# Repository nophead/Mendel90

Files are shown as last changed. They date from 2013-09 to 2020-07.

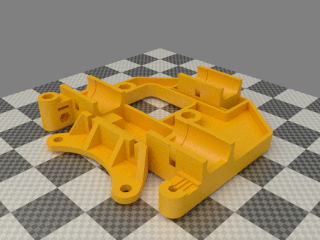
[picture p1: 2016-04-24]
dibond/render/printed/x_carriage_parts.png

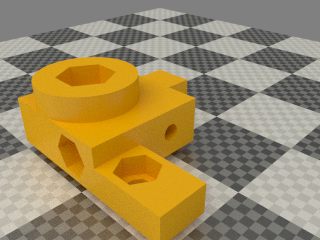
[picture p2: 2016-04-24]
dibond/render/printed/cal.png

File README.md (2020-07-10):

# A RepRap Mendel variant using sheets for the frame instead of rods

## Standard variants
[dibond](https://github.com/nophead/Mendel90/tree/master/dibond) is the version that was sold as a kit with 3mm sheets, 8mm rods and uses nuts and machine screws through the frame.

[sturdy](https://github.com/nophead/Mendel90/tree/master/sturdy) is 12mm MDF sheets, 10mm rods and uses wood screws into pilot holes in the frame. It can be built without CNC.

[mendel](https://github.com/nophead/Mendel90/tree/master/mendel) is 6mm acrylic sheets with a 10mm acrylic base, 8mm rods and uses machine screws into tapped holes in the frame.

[huxley](https://github.com/nophead/Mendel90/tree/master/huxley) is a scaled down version of dibond using 6mm rods and NEMA14 motors.

The dibond, sturdy and mendel versions can be modified to accept the E3D v6 hot end. The files that change are [dibond_E3D](https://github.com/nophead/Mendel90/tree/master/dibond_E3D)
and [sturdy_E3D](https://github.com/nophead/Mendel90/tree/master/sturdy_E3D).

## Limitations
The dibond and sturdy versions are well tested and popular. The acrylic version, called mendel, hasn't been built for a long time and is not recommened.
The Huxley version hasn't been tested in its final form although one prototype has been made of an earlier version and a few snags fixed since.

## Use
Add the directory of the OpenScad executable to your search path. OpenSCAD-2015.05 or later is required.
To get PDF versions of the sheet drawings add InkScape to your search path.

To make all the files for a machine run
```python
make_machine.py machine_name
```

To make just the bom, sheets or stls run bom.py, sheets.py or stls.py machine\_name.

machine\_name can be dibond, mendel, sturdy or huxley. To make your own variant copy scad\conf\mendel\_config.scad or scad\conf\sturdy\_config.scad to yourname\_config.scad.  Then run `make_machine.py yourname`.

To view the model of the whole machine, open scad\main.scad. It will take several minutes to render (about about 5 minutes on my computer) but after that you can pan and zoom it at reasonable speed and changes takes less time to render.  (Note: main.scad will only render correctly if conf\machine.scad exists, which is created by the make_machine.py script.)

To view a sub-assembly, open the individual scad files. Set the exploded flag in config.scad to make exploded views.

To get blender renders of all the parts put blender in your search path and run `render.py machine_name`.

## Credits
Fan model based on [this model](http://www.thingiverse.com/thing:8063) by MiseryBot, CC license.

[Sanguinololu model](http://www.thingiverse.com/thing:18606) by ax\_the\_b, CC license.

Spring taken from openscad example 20

x-end.scad and wade.scad use some elements of the Prusa ones by Josef Prusa, GPL license.

z_couplings originally based on [this model](http://www.thingiverse.com/thing:7153) by Griffin_Nicoll, GPL license.

Bearing holders originally based on [this model](http://www.thingiverse.com/thing:7755) by Jolijar, CC license.

InkCL.py based on [this code](http://kaioa.com/node/42)

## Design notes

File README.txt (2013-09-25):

Limitations
-----------
Currently only supports mendel and sturdy machine variants, the huxley version needs more work.

Use
---
Add the directory of the OpenScad executable to your search path. OpenSCAD-2013.06 or later is required.
To get PDF versions of the sheet drawings add InkScape to your search path.

To make all the files for a machine run
    make_machine.py machine_name

To make just the bom, sheets or stls run bom.py, sheets.py or stls.py machine_name.

machine_name can be mendel or sturdy. To make your own variant copy scad\conf\mendel_config.scad or scad\conf\sturdy_config.scad to yourname_config.scad.  Then run make_machine yourname.

To view the model of the whole machine, open scad\main.scad. It will take several minutes to render (about about 8 minutes on my computer) but after that you can pan and zoom it at reasonable speed and changes takes less time to render.  (Note: main.scad will only render correctly if conf\machine.scad exists, which is created by the make_machine.py script.)

To view a sub-assembly, open the individual scad files. Set the exploded flag in config.scad to make exploded views.

To get blender renders of all the parts put blender in your search path and run render.py machine_name.

Credits
-------
Fan model based on http://www.thingiverse.com/thing:8063 by MiseryBot, CC license.

Sanguinololu model http://www.thingiverse.com/thing:18606 by ax_the_b, CC license.

Spring taken from openscad example 20

x-end.scad and wade.scad use some elements of the Prusa ones by Josef Prusa, GPL license.

z_couplings originally based on http://www.thingiverse.com/thing:7153 by Griffin_Nicoll, GPL license.

Bearing holders originally based on http://www.thingiverse.com/thing:7755 by Jolijar, CC license.

InkCL.py based on code from http://kaioa.com/node/42

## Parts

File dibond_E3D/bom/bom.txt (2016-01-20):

Vitamins:
          E                                                      
          x                                                      
          t                                                      
          r                                                      
          u                                                      
          d                                                      
          e                                                      
          r                                                      
                                                                 
          c  E                          X                        
          o  x                                                   
          n  t                 S        c                        
    E     n  r                 p        a                        
    l     e  u                 o     X  r           Y            
    e     c  d           P     o        r                        
    c  E  t  e           r     l     c  i           c            
 B  t  x  i  r     H  M  i           a  a  X  X     a  Y  Y     Z
 e  r  t  o        o  a  n     h  X  r  g        Y  r        Z   
 d  o  r  n  m  F  t  c  t     o     r  e  i  m     r  i  m     m
    n  u     o  r     h        l  a  i     d  o  a  i  d  o  a  o
 f  i  d  p  t  a  e  i  b  P  d  x  a  f  l  t  x  a  l  t  x  t
 a  c  e  c  o  m  n  n  e  s  e  i  g  a  e  o  i  g  e  o  i  o
 n  s  r  b  r  e  d  e  d  u  r  s  e  n  r  r  s  e  r  r  s  r
  |  |  |  |  |  |  |  |  | 1|  |  |  |  |  |  |  |  |  |  |  |  |  1 THS15 Aluminium clad resistor 10R
  |  |  |  |  |  |  |  |  | 1|  |  |  |  |  |  |  |  |  |  |  |  |  1 THS15 Aluminium clad resistor 4R7
  |  |  |  |  |  |  |  |  | 1|  |  |  |  |  |  |  |  |  |  |  |  |  1 PSU e.g. ALPINE500
  |  | 3|  |  |  |  |  |  |  | 4|  |  |  |  |  |  |  |  |  |  |  |  7 Ball bearing 608 8mm x 22mm x 7mm
  |  |  |  |  |  |  |  |  |  |  |  |  |  | 2|  |  |  | 2|  |  |  |  4 Ball bearing 624 4mm x 13mm x 5mm
  |  |  |  |  |  |  |  | 4|  |  |  |  |  |  |  |  |  |  |  |  |  |  4 19mm bulldog clip
  |  |  |  |  |  |  |  | 1|  |  |  |  |  |  |  |  |  |  |  |  |  |  1 PCB bed 214mm x 214mm
  |  |  |  |  |  |  |  |  |  |  |  |  |  |  |  | 1|  |  |  |  |  |  1 Belt T2 x 6mm x 662mm
  |  |  |  |  |  |  |  |  |  |  | 1|  |  |  |  |  |  |  |  |  |  |  1 Belt T2 x 6mm x 860mm
  |  |  |  |  |  |  |  | 4|  |  |  |  |  |  |  |  |  |  |  |  |  |  4 Corrugated cardboard 201mm x 216mm x 5mm
  |  |  |  |  |  |  |  | 4|  |  |  |  |  |  |  |  |  |  |  |  |  |  4 M3 cap screw x 10mm
  |  | 3|  |  |  |  |  |  |  |  |  |  |  |  |  |  |  |  |  |  |  |  3 M3 cap screw x 12mm
  | 4|  |  |  |  |  |  |  |  |  |  | 2|  |  | 6| 4|14|  |  | 2| 2| 34 M3 cap screw x 16mm
  |  |  |  |  |  |  |  |  |  |  |  | 1|  | 8|10|  | 2|  |  |  | 8| 29 M3 cap screw x 20mm
  |  |  |  |  |  |  |  |  |  |  |  | 2|  |  |  |  |  |  |  |  |  |  2 M3 cap screw x 25mm
  |  |  |  | 2|  |  |  |  |  |  |  |  |  |  | 2|  |  |  |  |  |  |  4 M3 cap screw x 45mm
 4|  |  |  |  |36|  |  |  | 4| 2|  |  |  |  |  | 8|  | 1| 4| 4| 4| 67 M4 cap screw x 16mm
  |  |  |  |  |  |  |  |  |  |  |  |  | 4|  |  |  |  | 1|  |  |  |  5 M4 cap screw x 30mm
  |  |  |  |  |  |  |  |  |  |  |  |  |  | 1|  |  |  |  |  |  |  |  1 M4 cap screw x 45mm
  |  |  |  |  |  |  |  |  |  | 4|  |  |  |  |  |  |  |  |  |  |  |  4 M8 cap screw x 30mm
  |  |  |  |  | 2|  |  |  |  |  |  |  |  |  |  |  |  |  |  |  |  |  2 Dibond sheet 166mm x 388mm x 3mm
  |  |  |  |  |  |  |  |  |  |  |  |  |  |  |  |  | 1|  |  |  |  |  1 Dibond sheet 216mm x 216mm x 3mm
  |  |  |  |  | 1|  |  |  |  |  |  |  |  |  |  |  |  |  |  |  |  |  1 Dibond sheet 465mm x 388mm x 3mm
  |  |  |  |  | 1|  |  |  |  |  |  |  |  |  |  |  |  |  |  |  |  |  1 Dibond sheet 465mm x 419mm x 3mm
  |  |  | 1|  |  |  |  |  |  |  |  |  |  |  |  |  |  |  |  |  |  |  1 15 way D PCB mount plug
  |  |  |  |  |  |  |  |  |  |  |  |  |  |  | 1|  |  |  |  |  |  |  1 15 way D IDC socket
  |  |  |  |  |  | 1|  |  |  |  |  |  |  |  |  |  |  |  |  |  |  |  1 Fan 30mm x 10mm
  |  |  |  |  |  |  |  |  |  |  |  |  | 1|  |  |  |  |  |  |  |  |  1 Fan 60mm x 15mm
  |  |  |  |  |  |  |  |  |  | 1|  |  |  |  |  |  |  |  |  |  |  |  1 Foam sponge 20mm x 20mm x 20mm
  |  |  |  | 1|  |  |  |  |  |  |  |  |  |  | 2|  |  |  | 2|  |  |  5 M3 grub screw x 6mm
  |  |  |  |  |  |  |  | 1|  |  |  |  |  |  |  |  |  |  |  |  |  |  1 Glass sheet 214mm x 202mm x 2mm
  |  |  |  |  |  | 1|  |  |  |  |  |  |  |  |  |  |  |  |  |  |  |  1 E3D V6 direct 3mm
  |  |  |  |  |  |  |  | 4|  |  |  |  |  |  |  |  |  |  |  |  |  |  4 Hex male / female pillar M3 x 20mm
  |  | 3|  |  |  |  |  |  |  |  |  |  |  |  |  |  |  |  |  |  |  |  3 M3 hex screw x 10mm
  |  | 1|  |  |  |  |  |  |  |  | 1|  |  |  |  |  |  |  |  |  |  |  2 M4 hex screw x 20mm
  |  | 2|  |  |  |  |  |  |  |  |  |  |  |  |  |  |  |  |  |  |  |  2 M4 hex screw x 50mm
  |  | 1|  |  |  |  |  |  |  |  |  |  |  |  |  |  |  |  |  |  |  |  1 M8 hex screw x 60mm, hobbed at 25
  |  |  |  |  |  |  |  |  | 1|  |  |  |  |  |  |  |  |  |  |  |  |  1 IEC mains lead
  |  |  |  |  |  |  |  |  |  |  |  | 3|  | 2| 2|  | 3|  |  |  |  | 10 LM8UU linear bearing
  | 1|  |  |  |  |  |  |  |  |  |  |  |  |  |  |  |  |  |  |  |  |  1 Melzi electronics
  |  |  | 1|  |  |  |  |  |  |  |  |  |  |  |  |  |  |  |  |  |  |  1 2 way Molex KK header
  |  |  | 1|  |  |  |  |  |  |  |  |  |  |  |  |  |  |  |  |  |  |  1 3 way Molex KK header
  |  |  |  | 1|  |  |  |  |  |  |  |  |  |  | 1|  |  |  | 1|  | 2|  5 NEMA17 x 47mm stepper motor
  |  |  |  |  |  |  |  |  |  |  |  |  |  |  |  |  |  |  |  | 2|  |  2 Brass nut M6
  |  | 3|  | 3|  |  |  |  |  |  |  | 1|  |  |  |  |  |  |  |  |  |  7 Nut M3
  |  | 3|  |  |  |  |  |  |  |  |  |  |  |  |  |  |  |  |  |  |  |  3 Nut M4
  |  | 2|  |  |  |  |  |  |  |  |  |  |  |  |  |  |  |  |  |  |  |  2 Nut M8
  |  |  |  |  |  |  |  |  | 4|  |  |  |  |  |  |  |  |  |  |  |  |  4 Nyloc nut M2.5
  | 4|  |  |  |  |  |  |  |  |  |  | 4|  | 8|14| 4|16|  |  | 2|10| 62 Nyloc nut M3
 4|  |  |  |  |36|  |  |  | 4| 2|  |  | 4| 1|  | 8|  | 2| 4| 4| 4| 73 Nyloc nut M4
  |  |  |  |  |  |  |  |  |  | 4|  |  |  |  |  |  |  |  |  |  |  |  4 Nyloc nut M8
  |  |  |  |  |  |  |  |  |  |  |  |  |  |  | 2|  |  |  |  |  |  |  2 Nitrile O-ring 2.5mm x 1.6mm
  |  |  | 1|  |  |  |  |  |  |  |  |  |  |  |  |  |  |  |  |  |  |  1 Extruder connection PCB
  |  |  |  |  |  |  |  |  |  | 1|  |  |  |  |  |  |  |  |  |  |  |  1 PLA sample 3mm ~50m
  |  |  |  |  |  |  |  |  |  |  |  |  |  |  | 1|  |  |  |  |  |  |  1 Polypropylene strip 394mm x 18mm x 0.5mm
  |  |  |  |  |  |  |  |  |  |  |  |  |  |  | 1|  |  |  |  |  |  |  1 Polypropylene strip 456mm x 25mm x 0.5mm
  |  |  |  |  |  |  |  | 1|  |  |  |  |  |  |  |  |  |  |  |  |  |  1 Polypropylene strip 271mm x 33mm x 0.5mm
  |  |  |  |  |  |  |  |  | 4|  |  |  |  |  |  |  |  |  |  |  |  |  4 M2.5 pan screw x 12mm
  |  |  |  |  |  |  |  |  |  |  |  |  |  |  | 2|  |  |  | 4|  | 8| 14 M3 pan screw x 8mm
  |  |  |  |  |  |  |  |  | 2|  |  |  |  |  |  |  |  |  |  |  |  |  2 6-32 pan screw x 9.5mm
  |  |  |  | 2|  |  |  |  |  |  |  |  |  |  | 4| 2|  |  |  | 2|  | 10 No2 pan wood screw x 13mm
  |  |  |  |  |  |  |  |  |  |  |  |  |  |  | 1|  |  |  | 1|  |  |  2 GT2 pulley 20 teeth
  |  |  |  |  |  |  |  |  |  |  |  |  |  |  | 1|  |  |  |  |  |  |  1 Ribbon cable 20 way 1220mm
  |  |  |  |  |  |  |  | 1|  |  |  |  |  |  |  |  |  |  |  |  |  |  1 Ribbon cable 26 way 381mm
  |  | 1|  |  |  |  |  |  |  |  |  |  |  |  |  |  |  |  |  |  |  |  1 Smooth rod 8mm x 22mm
  |  |  |  |  |  |  |  |  |  |  |  |  |  |  |  | 1|  |  |  |  |  |  1 Smooth rod 8mm x 270mm
  |  |  |  |  |  |  |  |  |  |  |  |  |  |  |  |  |  |  |  | 2|  |  2 Smooth rod 8mm x 340mm
  |  |  |  |  |  |  |  |  |  |  | 2|  |  |  |  |  |  |  |  |  |  |  2 Smooth rod 8mm x 381mm
  |  |  |  |  |  |  |  |  |  |  |  |  |  |  |  | 1|  |  |  |  |  |  1 Smooth rod 8mm x 417mm
  | 1|  |  |  |  |  |  |  |  |  |  |  |  |  |  |  |  |  |  |  |  |  1 Micro SD card
  | 1|  |  |  |  |  |  |  |  |  |  |  |  |  |  |  |  |  |  |  |  |  1 Micro SD to USB adapter
  |  |  |  |  |  |  |  |  |  |  |  |  |  |  | 1| 1|  |  |  | 1|  |  3 Microswitch
  |  | 2|  |  |  |  |  |  |  |  |  |  |  |  |  |  |  |  |  |  |  |  2 Spring 7mm OD, 1mm gauge x 10mm long
  |  |  |  |  | 2|  |  |  |  |  |  |  |  |  |  |  |  |  |  |  |  |  2 AL square tube 12.7 x 12.7 x 1.63 x 400mm
  |  |  |  |  |  |  |  |  |  |  |  |  |  |  |  |  |  |  |  | 2|  |  2 Threaded rod M6 x 300mm
  |  |  |  |  |  |  |  |  | 1|  |  |  |  |  |  |  |  |  |  |  |  |  1 Heatshrink sleeving ID 10mm x 15mm
  |  |  |  |  |  |  |  | 2|  |  |  |  |  |  |  |  |  |  |  |  |  |  2 Heatshrink sleeving ID 1.6mm x 15mm
  | 2|  |  |  |  |  |  | 2| 3|  |  |  |  |  | 4|  |  |  |  |  |  | 11 Heatshrink sleeving ID 2.4mm x 15mm
  |  |  |  |  |  |  |  |  | 5|  |  |  |  |  |  |  |  |  |  |  |  |  5 Heatshrink sleeving ID 3.2mm x 15mm
  |  |  |  |  |  |  |  |  |  | 1|  |  |  |  |  |  |  |  |  |  |  |  1 PTFE tubing OD 4.6mm ID 3.84mm x 750mm
  |  |  |  |  |  |  |  |  | 2|  |  |  |  |  |  |  |  |  |  |  |  |  2 Heatshrink sleeving ID 6.4mm x 15mm
  |  |  |  |  |  |  |  | 2|  |  |  |  |  |  |  |  |  |  |  |  |  |  2 Heatshrink sleeving ID 6.4mm x 30mm
  |  |  |  |  |  | 1|  |  |  |  |  |  |  |  |  |  |  |  |  |  |  |  1 Heatshrink sleeving ID 6.4mm x 60mm
  |  |  |  |  |  |  |  |  |  |  |  |  |  |  |  |  |  |  |  |  | 2|  2 Neoprene tubing OD 8mm ID 5mm x 16mm
  |  |  | 2|  |  |  |  |  |  |  |  |  |  |  |  |  |  |  |  |  |  |  2 4 way terminal block
  |  |  |  |  |  |  |  | 1|  |  |  |  |  |  |  |  |  |  |  |  |  |  1 Epcos B57861S104F40 100K 1% thermistor
  | 1|  |  |  |  |  |  |  |  |  |  |  |  |  |  |  |  |  |  |  |  |  1 USB A to Mini B lead
  |  |  |  | 2|  |  |  |  | 4|  |  |  |  |  | 4| 2|  |  |  | 2|  | 14 Washer M2.5 x 5.9mm x 0.5mm
  | 8| 3|  | 2|  |  |  | 4|  |  |  | 4|  | 8|22| 4|16|  | 4| 2|18| 95 Washer M3 x 7mm x 0.5mm
 4|  | 8|  |  |40|  |  |  | 6| 2|  |  | 4| 2|  | 8|  | 5| 4| 4| 4| 91 Washer M4 x 9mm x 0.8mm
  |  |  |  |  |  |  |  |  |  |  |  |  |  | 2|  |  |  | 2|  |  |  |  4 Washer M5 x 20mm x 1.4mm
  |  |  |  |  |  |  |  |  |  |12|  |  |  |  |  |  |  |  |  |  |  | 12 Washer M8 x 17mm x 1.6mm
  |  |  |  |  |  |  |  |  |  | 4|  |  |  |  |  |  |  |  |  |  |  |  4 Washer M8 x 30mm x 1.5mm
  |  |  |  |  |  |  |  |  |  |  | 1|  |  |  |  |  |  |  |  |  |  |  1 Wingnut M4
  |  |  |  |  |  |  |  | 1|  |  |  |  |  |  |  |  |  |  |  |  |  |  1 Black wire 32/0.2 length 635mm
  |  |  |  |  |  |  |  | 1|  |  |  |  |  |  |  |  |  |  |  |  |  |  1 Red wire 32/0.2 length 620mm
  |  | 6|  |  |  |  |  |  |  |  |  |  |  |  | 2|  |  |  | 4|  | 8| 20 Star washer M3 x 0.5mm
  |  |  |  |  |  |  |  |  | 2|  |  |  |  |  |  |  |  |  |  |  |  |  2 Star washer M4 x 0.8mm
  |  | 1|  |  |  |  |  |  |  |  |  |  |  |  |  |  |  |  |  |  |  |  1 Star washer M8 x 1.6mm
  |  |  |  |  |10| 1|  |  | 2|  |  | 3|  |  |  |  | 3|  |  |  |  | 19 Ziptie 100mm min length

Printed:
  |  |  |  |  |  |  |  |  | 1|  |  |  |  |  |  |  |  |  |  |  |  |  1 atx_long_bracket.stl
  |  |  |  |  |  |  |  |  | 1|  |  |  |  |  |  |  |  |  |  |  |  |  1 atx_short_bracket.stl
  |  |  |  | 1|  |  |  |  |  |  |  |  |  |  |  |  |  |  |  |  |  |  1 d_motor_bracket.stl
  |  |  |  | 1|  |  |  |  |  |  |  |  |  |  |  |  |  |  |  |  |  |  1 d_motor_bracket_lid.stl
  |  |  |  |  |  |  |  |  |  |  |  |  |  |  | 1|  |  |  |  |  |  |  1 d_shell.stl
  |  |  |  |  |  |  |  |  |  |  |  |  |  |  | 1|  |  |  |  |  |  |  1 d_shell_lid.stl
  |  |  |  |  |  |  |  |  |  | 1|  |  |  |  |  |  |  |  |  |  |  |  1 dust_filter.stl
 1|  |  |  |  |  |  |  |  |  |  |  |  |  |  |  |  |  |  |  |  |  |  1 fan_guard.stl
  |  |  |  |  | 8|  |  |  |  |  |  |  |  |  |  |  |  |  |  |  |  |  8 fixing_block.stl
  | 4|  |  |  |  |  |  |  |  |  |  |  |  |  |  |  |  |  |  |  |  |  4 pcb_spacer.stl
  |  |  |  |  | 2|  |  |  |  |  |  |  |  |  |  |  |  |  |  |  |  |  2 rear_fixing_block.stl
  |  |  |  |  |  |  |  |  |  |  |  |  |  |  | 1|  |  |  |  |  |  |  1 ribbon_clamp_14_33.stl
  |  |  |  |  |  |  |  |  |  |  |  |  |  |  | 1|  |  |  |  |  |  |  1 ribbon_clamp_14_33NB.stl
  |  |  |  |  |  |  |  |  |  |  |  |  |  |  | 1|  |  |  |  |  |  |  1 ribbon_clamp_20_33.stl
  |  |  |  |  | 1|  |  |  |  |  |  |  |  |  |  |  |  |  |  |  |  |  1 ribbon_clamp_20_44N.stl
  |  |  |  |  |  |  |  |  |  |  |  |  |  |  |  |  | 1|  |  |  |  |  1 ribbon_clamp_26_33.stl
  |  |  |  |  |  |  |  |  |  |  |  |  |  |  |  |  | 1|  |  |  |  |  1 ribbon_clamp_26_33N.stl
  |  |  |  |  | 1|  |  |  |  |  |  |  |  |  |  |  |  |  |  |  |  |  1 ribbon_clamp_26_44N.stl
  |  |  |  |  |  |  |  |  |  | 2|  |  |  |  |  |  |  |  |  |  |  |  2 spool_bracket_female.stl
  |  |  |  |  |  |  |  |  |  | 2|  |  |  |  |  |  |  |  |  |  |  |  2 spool_bracket_male.stl
  |  |  |  |  | 4|  |  |  |  |  |  |  |  |  |  |  |  |  |  |  |  |  4 tube_cap.stl
  |  | 1|  |  |  |  |  |  |  |  |  |  |  |  |  |  |  |  |  |  |  |  1 wades_big_gear.stl
  |  | 1|  |  |  |  |  |  |  |  |  |  |  |  |  |  |  |  |  |  |  |  1 wades_block.stl
  |  | 1|  |  |  |  |  |  |  |  |  |  |  |  |  |  |  |  |  |  |  |  1 wades_gear_spacer.stl
  |  | 1|  |  |  |  |  |  |  |  |  |  |  |  |  |  |  |  |  |  |  |  1 wades_idler_block.stl
  |  |  |  | 1|  |  |  |  |  |  |  |  |  |  |  |  |  |  |  |  |  |  1 wades_small_gear.stl
  |  |  |  |  |  |  |  |  |  |  |  | 1|  |  |  |  |  |  |  |  |  |  1 x_belt_clamp.stl
  |  |  |  |  |  |  |  |  |  |  |  | 1|  |  |  |  |  |  |  |  |  |  1 x_belt_grip.stl
  |  |  |  |  |  |  |  |  |  |  |  | 1|  |  |  |  |  |  |  |  |  |  1 x_belt_tensioner.stl
  |  |  |  |  |  |  |  |  |  |  |  | 1|  |  |  |  |  |  |  |  |  |  1 x_carriage.stl
  |  |  |  |  |  |  |  |  |  |  |  |  | 1|  |  |  |  |  |  |  |  |  1 x_carriage_fan_bracket.stl
  |  |  |  |  |  |  |  |  |  |  |  |  | 1|  |  |  |  |  |  |  |  |  1 x_carriage_fan_duct.stl
  |  |  |  |  |  |  |  |  |  |  |  |  |  | 2| 2|  |  |  |  |  |  |  4 x_end_clamp.stl
  |  |  |  |  |  |  |  |  |  |  |  |  |  | 1|  |  |  |  |  |  |  |  1 x_idler_bracket.stl
  |  |  |  |  |  |  |  |  |  |  |  |  |  |  | 1|  |  |  |  |  |  |  1 x_motor_bracket.stl
  |  |  |  |  |  |  |  |  |  |  |  |  |  |  | 1|  |  |  |  |  |  |  1 x_motor_ribbon_bracket.stl
  |  |  |  |  |  |  |  |  |  |  |  |  |  |  |  | 3|  |  |  |  |  |  3 y_bar_clamp.stl
  |  |  |  |  |  |  |  |  |  |  |  |  |  |  |  | 1|  |  |  |  |  |  1 y_bar_clamp_switch.stl
  |  |  |  |  |  |  |  |  |  |  |  |  |  |  |  |  | 3|  |  |  |  |  3 y_bearing_mount.stl
  |  |  |  |  |  |  |  |  |  |  |  |  |  |  |  |  | 1|  |  |  |  |  1 y_belt_anchor.stl
  |  |  |  |  |  |  |  |  |  |  |  |  |  |  |  |  | 1|  |  |  |  |  1 y_belt_anchor_toothed.stl
  |  |  |  |  |  |  |  |  |  |  |  |  |  |  |  |  | 1|  |  |  |  |  1 y_belt_clip.stl
  |  |  |  |  |  |  |  |  |  |  |  |  |  |  |  |  | 1|  |  |  |  |  1 y_belt_clip_toothed.stl
  |  |  |  |  |  |  |  |  |  |  |  |  |  |  |  |  |  | 1|  |  |  |  1 y_idler_bracket.stl
  |  |  |  |  |  |  |  |  |  |  |  |  |  |  |  |  |  |  | 1|  |  |  1 y_motor_bracket.stl
  |  |  |  |  |  |  |  |  |  |  |  |  |  |  |  |  |  |  |  | 2|  |  2 z_bar_clamp.stl
  |  |  |  |  |  |  |  |  |  |  |  |  |  |  |  |  |  |  |  |  | 4|  4 z_coupling.stl
  |  |  |  |  |  |  |  |  |  |  |  |  |  |  |  |  |  |  |  |  | 1|  1 z_motor_bracket_lhs.stl
  |  |  |  |  |  |  |  |  |  |  |  |  |  |  |  |  |  |  |  |  | 1|  1 z_motor_bracket_rhs.stl
  |  |  |  |  |  |  |  |  |  |  |  |  |  |  |  |  |  |  |  | 2|  |  2 z_screw_pointer.stl

Sub-assemblies:
  1 bed_fan_assembly
  1 electronics_assembly
  1 extruder_assembly
  1 extruder_connection_pcb_assembly
  1 extruder_motor_assembly
  1 frame_assembly
  1 hot_end_assembly
  1 machine_assembly
  1 print_bed_assembly
  1 psu_assembly
  1 spool_holder_assembly
  1 x_axis_assembly
  1 x_carriage_assembly
  1 x_carriage_fan_assembly
  1 x_idler_assembly
  1 x_motor_assembly
  1 y_axis_assembly
  1 y_carriage_assembly
  1 y_idler_assembly
  1 y_motor_assembly
  1 z_axis_assembly
  2 z_motor_assemblies

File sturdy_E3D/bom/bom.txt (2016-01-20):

Vitamins:
          E                                                      
          x                                                      
          t                                                      
          r                                                      
          u                                                      
          d                                                      
          e                                                      
          r                                                      
                                                                 
          c  E                          X                        
          o  x                                                   
          n  t                 S        c                        
    E     n  r                 p        a                        
    l     e  u                 o     X  r           Y            
    e     c  d           P     o        r                        
    c  E  t  e           r     l     c  i           c            
 B  t  x  i  r     H  M  i           a  a  X  X     a  Y  Y     Z
 e  r  t  o        o  a  n     h  X  r  g        Y  r        Z   
 d  o  r  n  m  F  t  c  t     o     r  e  i  m     r  i  m     m
    n  u     o  r     h        l  a  i     d  o  a  i  d  o  a  o
 f  i  d  p  t  a  e  i  b  P  d  x  a  f  l  t  x  a  l  t  x  t
 a  c  e  c  o  m  n  n  e  s  e  i  g  a  e  o  i  g  e  o  i  o
 n  s  r  b  r  e  d  e  d  u  r  s  e  n  r  r  s  e  r  r  s  r
  |  |  |  |  |  |  |  |  | 1|  |  |  |  |  |  |  |  |  |  |  |  |  1 THS15 Aluminium clad resistor 10R
  |  |  |  |  |  |  |  |  | 1|  |  |  |  |  |  |  |  |  |  |  |  |  1 THS15 Aluminium clad resistor 4R7
  |  |  |  |  |  |  |  |  | 1|  |  |  |  |  |  |  |  |  |  |  |  |  1 PSU e.g. ALPINE500
  |  | 3|  |  |  |  |  |  |  | 4|  |  |  |  |  |  |  |  |  |  |  |  7 Ball bearing 608 8mm x 22mm x 7mm
  |  |  |  |  |  |  |  |  |  |  |  |  |  | 2|  |  |  | 2|  |  |  |  4 Ball bearing 624 4mm x 13mm x 5mm
  |  |  |  |  |  |  |  | 4|  |  |  |  |  |  |  |  |  |  |  |  |  |  4 19mm bulldog clip
  |  |  |  |  |  |  |  | 1|  |  |  |  |  |  |  |  |  |  |  |  |  |  1 PCB bed 214mm x 214mm
  |  |  |  |  |  |  |  |  |  |  |  |  |  |  |  | 1|  |  |  |  |  |  1 Belt T2 x 6mm x 680mm
  |  |  |  |  |  |  |  |  |  |  | 1|  |  |  |  |  |  |  |  |  |  |  1 Belt T2 x 6mm x 904mm
  |  |  |  |  |  |  |  | 4|  |  |  |  |  |  |  |  |  |  |  |  |  |  4 Corrugated cardboard 201mm x 217mm x 5mm
  |  |  |  |  |  |  |  | 4|  |  |  |  |  |  |  |  |  |  |  |  |  |  4 M3 cap screw x 10mm
  |  | 3|  |  |  |  |  |  |  |  |  |  |  |  |  |  |  |  |  |  |  |  3 M3 cap screw x 12mm
  | 4|  |  |  |  |  |  |  |  |  |  | 2|  |  | 6|  | 8|  |  |  |  | 20 M3 cap screw x 16mm
  |  |  |  |  |  |  |  |  |  |  |  | 1|  | 8|10|  |  |  |  |  | 8| 27 M3 cap screw x 20mm
  |  |  |  |  |  |  |  |  |  |  |  | 2|  |  |  |  |  |  |  |  |  |  2 M3 cap screw x 25mm
  |  |  |  | 2|  |  |  |  |  |  |  |  |  |  | 2|  |  |  |  |  |  |  4 M3 cap screw x 45mm
  |  |  |  |  |  |  |  |  |  |  |  |  |  |  |  |  | 6|  |  |  |  |  6 M4 cap screw x 16mm
  |  |  |  |  |  |  |  |  |  |  |  |  |  |  |  | 4| 2|  |  | 2| 2| 10 M4 cap screw x 20mm
 4|  |  |  |  |  |  |  |  |  |  |  |  |  |  |  |  |  |  |  |  |  |  4 M4 cap screw x 25mm
  |  |  |  |  |  |  |  |  |  |  |  |  | 4|  |  |  |  | 1|  |  |  |  5 M4 cap screw x 30mm
  |  |  |  |  |  |  |  |  |  |  |  |  |  | 1|  |  |  |  |  |  |  |  1 M4 cap screw x 45mm
  |  |  |  |  |  |  |  |  |  | 4|  |  |  |  |  |  |  |  |  |  |  |  4 M8 cap screw x 30mm
  |  |  |  |  |  |  |  |  |  |  |  |  |  |  |  |  | 1|  |  |  |  |  1 Dibond sheet 217mm x 217mm x 3mm
  |  |  | 1|  |  |  |  |  |  |  |  |  |  |  |  |  |  |  |  |  |  |  1 15 way D PCB mount plug
  |  |  |  |  |  |  |  |  |  |  |  |  |  |  | 1|  |  |  |  |  |  |  1 15 way D IDC socket
  |  |  |  |  |  | 1|  |  |  |  |  |  |  |  |  |  |  |  |  |  |  |  1 Fan 30mm x 10mm
  |  |  |  |  |  |  |  |  |  |  |  |  | 1|  |  |  |  |  |  |  |  |  1 Fan 60mm x 15mm
  |  |  |  |  |  |  |  |  |  | 1|  |  |  |  |  |  |  |  |  |  |  |  1 Foam sponge 20mm x 20mm x 20mm
  |  |  |  | 1|  |  |  |  |  |  |  |  |  |  | 2|  |  |  | 2|  |  |  5 M3 grub screw x 6mm
  |  |  |  |  |  |  |  | 1|  |  |  |  |  |  |  |  |  |  |  |  |  |  1 Glass sheet 214mm x 202mm x 2mm
  |  |  |  |  |  | 1|  |  |  |  |  |  |  |  |  |  |  |  |  |  |  |  1 E3D V6 direct 3mm
  |  |  |  |  |  |  |  | 4|  |  |  |  |  |  |  |  |  |  |  |  |  |  4 Hex male / female pillar M3 x 20mm
  |  | 3|  |  |  |  |  |  |  |  |  |  |  |  |  |  |  |  |  |  |  |  3 M3 hex screw x 10mm
  |  | 1|  |  |  |  |  |  |  |  | 1|  |  |  |  |  |  |  |  |  |  |  2 M4 hex screw x 20mm
  |  | 2|  |  |  |  |  |  |  |  |  |  |  |  |  |  |  |  |  |  |  |  2 M4 hex screw x 50mm
  |  | 1|  |  |  |  |  |  |  |  |  |  |  |  |  |  |  |  |  |  |  |  1 M8 hex screw x 60mm, hobbed at 25
  |  |  |  |  |  |  |  |  | 1|  |  |  |  |  |  |  |  |  |  |  |  |  1 IEC mains lead
  |  |  |  |  |  |  |  |  |  |  |  | 3|  | 2| 2|  | 3|  |  |  |  | 10 LM10UU linear bearing
  |  |  |  |  | 2|  |  |  |  |  |  |  |  |  |  |  |  |  |  |  |  |  2 MDF sheet 162mm x 389mm x 12mm
  |  |  |  |  | 1|  |  |  |  |  |  |  |  |  |  |  |  |  |  |  |  |  1 MDF sheet 489mm x 389mm x 12mm
  |  |  |  |  | 1|  |  |  |  |  |  |  |  |  |  |  |  |  |  |  |  |  1 MDF sheet 489mm x 436mm x 12mm
  | 1|  |  |  |  |  |  |  |  |  |  |  |  |  |  |  |  |  |  |  |  |  1 Melzi electronics
  |  |  | 1|  |  |  |  |  |  |  |  |  |  |  |  |  |  |  |  |  |  |  1 2 way Molex KK header
  |  |  | 1|  |  |  |  |  |  |  |  |  |  |  |  |  |  |  |  |  |  |  1 3 way Molex KK header
  |  |  |  | 1|  |  |  |  |  |  |  |  |  |  | 1|  |  |  | 1|  | 2|  5 NEMA17 x 47mm stepper motor
  |  |  |  |  |  |  |  |  |  |  |  |  |  |  |  |  |  |  |  | 2|  |  2 Brass nut M8
  |  | 3|  | 3|  |  |  |  |  |  |  | 1|  |  |  |  |  |  |  |  |  |  7 Nut M3
  |  | 3|  |  |  |  |  |  |  |  |  |  |  |  |  |  |  |  |  |  |  |  3 Nut M4
  |  | 2|  |  |  |  |  |  |  |  |  |  |  |  |  |  |  |  |  |  |  |  2 Nut M8
  |  |  |  |  |  |  |  |  |  |  |  | 4|  | 8|14|  | 8|  |  |  | 8| 42 Nyloc nut M3
 4|  |  |  |  |  |  |  |  |  |  |  |  | 4| 1|  | 4| 8| 1|  | 2| 2| 26 Nyloc nut M4
  |  |  |  |  |  |  |  |  |  | 4|  |  |  |  |  |  |  |  |  |  |  |  4 Nyloc nut M8
  |  |  |  |  |  |  |  |  |  |  |  |  |  |  | 2|  |  |  |  |  |  |  2 Nitrile O-ring 2.5mm x 1.6mm
  |  |  | 1|  |  |  |  |  |  |  |  |  |  |  |  |  |  |  |  |  |  |  1 Extruder connection PCB
  |  |  |  |  |  |  |  |  |  | 1|  |  |  |  |  |  |  |  |  |  |  |  1 PLA sample 3mm ~50m
  |  |  |  |  |  |  |  |  |  |  |  |  |  |  | 1|  |  |  |  |  |  |  1 Polypropylene strip 410mm x 18mm x 0.5mm
  |  |  |  |  |  |  |  |  |  |  |  |  |  |  | 1|  |  |  |  |  |  |  1 Polypropylene strip 501mm x 25mm x 0.5mm
  |  |  |  |  |  |  |  | 1|  |  |  |  |  |  |  |  |  |  |  |  |  |  1 Polypropylene strip 278mm x 33mm x 0.5mm
  |  |  |  |  |  |  |  |  |  |  |  |  |  |  | 2|  |  |  | 4|  | 8| 14 M3 pan screw x 8mm
  |  |  |  |  |  |  |  |  | 2|  |  |  |  |  |  |  |  |  |  |  |  |  2 6-32 pan screw x 9.5mm
  |  |  |  | 2|  |  |  |  | 4|  |  |  |  |  | 4| 2|  |  |  | 2|  | 14 No2 pan wood screw x 13mm
  |  |  |  |  |39|  |  |  | 4| 2|  |  |  |  |  | 8|  | 1| 4| 4| 4| 66 No6 pan wood screw x 16mm
  |  |  |  |  |  |  |  |  |  |  |  |  |  |  | 1|  |  |  | 1|  |  |  2 GT2 pulley 20 teeth
  |  |  |  |  |  |  |  |  |  |  |  |  |  |  | 1|  |  |  |  |  |  |  1 Ribbon cable 20 way 1281mm
  |  |  |  |  |  |  |  | 1|  |  |  |  |  |  |  |  |  |  |  |  |  |  1 Ribbon cable 26 way 388mm
  |  |  |  |  |  |  |  |  |  |  |  |  |  |  |  | 1|  |  |  |  |  |  1 Smooth rod 10mm x 290mm
  |  |  |  |  |  |  |  |  |  |  |  |  |  |  |  |  |  |  |  | 2|  |  2 Smooth rod 10mm x 340mm
  |  |  |  |  |  |  |  |  |  |  | 2|  |  |  |  |  |  |  |  |  |  |  2 Smooth rod 10mm x 403mm
  |  |  |  |  |  |  |  |  |  |  |  |  |  |  |  | 1|  |  |  |  |  |  1 Smooth rod 10mm x 432mm
  |  | 1|  |  |  |  |  |  |  |  |  |  |  |  |  |  |  |  |  |  |  |  1 Smooth rod 8mm x 22mm
  | 1|  |  |  |  |  |  |  |  |  |  |  |  |  |  |  |  |  |  |  |  |  1 Micro SD card
  | 1|  |  |  |  |  |  |  |  |  |  |  |  |  |  |  |  |  |  |  |  |  1 Micro SD to USB adapter
  |  |  |  |  |  |  |  |  |  |  |  |  |  |  | 1| 1|  |  |  | 1|  |  3 Microswitch
  |  | 2|  |  |  |  |  |  |  |  |  |  |  |  |  |  |  |  |  |  |  |  2 Spring 7mm OD, 1mm gauge x 10mm long
  |  |  |  |  |  |  |  |  |  |  |  |  |  |  |  |  |  |  |  | 2|  |  2 Threaded rod M8 x 300mm
  |  |  |  |  |  |  |  |  | 1|  |  |  |  |  |  |  |  |  |  |  |  |  1 Heatshrink sleeving ID 10mm x 15mm
  |  |  |  |  |  |  |  | 2|  |  |  |  |  |  |  |  |  |  |  |  |  |  2 Heatshrink sleeving ID 1.6mm x 15mm
  | 2|  |  |  |  |  |  | 2| 3|  |  |  |  |  | 4|  |  |  |  |  |  | 11 Heatshrink sleeving ID 2.4mm x 15mm
  |  |  |  |  |  |  |  |  | 5|  |  |  |  |  |  |  |  |  |  |  |  |  5 Heatshrink sleeving ID 3.2mm x 15mm
  |  |  |  |  |  |  |  |  |  | 1|  |  |  |  |  |  |  |  |  |  |  |  1 PTFE tubing OD 4.6mm ID 3.84mm x 750mm
  |  |  |  |  |  |  |  |  | 2|  |  |  |  |  |  |  |  |  |  |  |  |  2 Heatshrink sleeving ID 6.4mm x 15mm
  |  |  |  |  |  |  |  | 2|  |  |  |  |  |  |  |  |  |  |  |  |  |  2 Heatshrink sleeving ID 6.4mm x 30mm
  |  |  |  |  |  | 1|  |  |  |  |  |  |  |  |  |  |  |  |  |  |  |  1 Heatshrink sleeving ID 6.4mm x 60mm
  |  |  |  |  |  |  |  |  |  |  |  |  |  |  |  |  |  |  |  |  | 2|  2 Neoprene tubing OD 8mm ID 5mm x 16mm
  |  |  | 2|  |  |  |  |  |  |  |  |  |  |  |  |  |  |  |  |  |  |  2 4 way terminal block
  |  |  |  |  |  |  |  | 1|  |  |  |  |  |  |  |  |  |  |  |  |  |  1 Epcos B57861S104F40 100K 1% thermistor
  | 1|  |  |  |  |  |  |  |  |  |  |  |  |  |  |  |  |  |  |  |  |  1 USB A to Mini B lead
  |  |  |  | 2|  |  |  |  |  |  |  |  |  |  | 4| 2|  |  |  | 2|  | 10 Washer M2.5 x 5.9mm x 0.5mm
  | 4| 3|  | 2|  |  |  | 4|  |  |  | 4|  | 8|22|  | 8|  | 4|  |16| 75 Washer M3 x 7mm x 0.5mm
 4|  | 8|  |  |39|  |  |  | 6| 2|  |  | 4| 2|  |12|14| 5| 4| 6| 6|112 Washer M4 x 9mm x 0.8mm
  |  |  |  |  |  |  |  |  |  |  |  |  |  | 2|  |  |  | 2|  |  |  |  4 Washer M5 x 20mm x 1.4mm
  |  |  |  |  |  |  |  |  |  |12|  |  |  |  |  |  |  |  |  |  |  | 12 Washer M8 x 17mm x 1.6mm
  |  |  |  |  |  |  |  |  |  | 4|  |  |  |  |  |  |  |  |  |  |  |  4 Washer M8 x 30mm x 1.5mm
  |  |  |  |  |  |  |  |  |  |  | 1|  |  |  |  |  |  |  |  |  |  |  1 Wingnut M4
  |  |  |  |  |  |  |  | 1|  |  |  |  |  |  |  |  |  |  |  |  |  |  1 Black wire 32/0.2 length 635mm
  |  |  |  |  |  |  |  | 1|  |  |  |  |  |  |  |  |  |  |  |  |  |  1 Red wire 32/0.2 length 620mm
  | 4| 6|  |  |  |  |  |  |  |  |  |  |  |  | 2|  |  |  | 4|  | 8| 24 Star washer M3 x 0.5mm
  |  |  |  |  |39|  |  |  | 6| 2|  |  |  |  |  | 8|  | 1| 4| 4| 4| 68 Star washer M4 x 0.8mm
  |  | 1|  |  |  |  |  |  |  |  |  |  |  |  |  |  |  |  |  |  |  |  1 Star washer M8 x 1.6mm
  |  |  |  |  |  | 1|  |  | 2|  |  |  |  |  |  |  |  |  |  |  |  |  3 Ziptie 100mm min length
  |  |  |  |  |  |  |  |  |  |  |  | 3|  |  |  |  | 3|  |  |  |  |  6 Ziptie 105mm min length

Printed:
  |  |  |  |  |  |  |  |  | 1|  |  |  |  |  |  |  |  |  |  |  |  |  1 atx_long_bracket.stl
  |  |  |  |  |  |  |  |  | 1|  |  |  |  |  |  |  |  |  |  |  |  |  1 atx_short_bracket.stl
  |  |  |  |  | 2|  |  |  |  |  |  |  |  |  |  |  |  |  |  |  |  |  2 cable_clip_AB.stl
  |  |  |  |  | 2|  |  |  |  |  |  |  |  |  |  |  |  |  |  |  |  |  2 cable_clip_AD.stl
  |  |  |  |  | 1|  |  |  |  |  |  |  |  |  |  |  |  |  |  |  |  |  1 cable_clip_CA.stl
  |  |  |  | 1|  |  |  |  |  |  |  |  |  |  |  |  |  |  |  |  |  |  1 d_motor_bracket.stl
  |  |  |  | 1|  |  |  |  |  |  |  |  |  |  |  |  |  |  |  |  |  |  1 d_motor_bracket_lid.stl
  |  |  |  |  |  |  |  |  |  |  |  |  |  |  | 1|  |  |  |  |  |  |  1 d_shell.stl
  |  |  |  |  |  |  |  |  |  |  |  |  |  |  | 1|  |  |  |  |  |  |  1 d_shell_lid.stl
  |  |  |  |  |  |  |  |  |  | 1|  |  |  |  |  |  |  |  |  |  |  |  1 dust_filter.stl
 1|  |  |  |  |  |  |  |  |  |  |  |  |  |  |  |  |  |  |  |  |  |  1 fan_guard.stl
  |  |  |  |  |10|  |  |  |  |  |  |  |  |  |  |  |  |  |  |  |  | 10 fixing_block.stl
  | 4|  |  |  |  |  |  |  |  |  |  |  |  |  |  |  |  |  |  |  |  |  4 pcb_spacer.stl
  |  |  |  |  |  |  |  |  |  |  |  |  |  |  | 1|  |  |  |  |  |  |  1 ribbon_clamp_14_33.stl
  |  |  |  |  |  |  |  |  |  |  |  |  |  |  | 1|  |  |  |  |  |  |  1 ribbon_clamp_14_33NB.stl
  |  |  |  |  |  |  |  |  |  |  |  |  |  |  | 1|  |  |  |  |  |  |  1 ribbon_clamp_20_33.stl
  |  |  |  |  | 1|  |  |  |  |  |  |  |  |  |  |  |  |  |  |  |  |  1 ribbon_clamp_20_40.stl
  |  |  |  |  | 1|  |  |  |  |  |  |  |  |  |  |  |  |  |  |  |  |  1 ribbon_clamp_26_40.stl
  |  |  |  |  |  |  |  |  |  |  |  |  |  |  |  |  | 1|  |  |  |  |  1 ribbon_clamp_26_44.stl
  |  |  |  |  |  |  |  |  |  |  |  |  |  |  |  |  | 1|  |  |  |  |  1 ribbon_clamp_26_44N.stl
  |  |  |  |  |  |  |  |  |  | 2|  |  |  |  |  |  |  |  |  |  |  |  2 spool_bracket_female.stl
  |  |  |  |  |  |  |  |  |  | 2|  |  |  |  |  |  |  |  |  |  |  |  2 spool_bracket_male.stl
  |  | 1|  |  |  |  |  |  |  |  |  |  |  |  |  |  |  |  |  |  |  |  1 wades_big_gear.stl
  |  | 1|  |  |  |  |  |  |  |  |  |  |  |  |  |  |  |  |  |  |  |  1 wades_block.stl
  |  | 1|  |  |  |  |  |  |  |  |  |  |  |  |  |  |  |  |  |  |  |  1 wades_gear_spacer.stl
  |  | 1|  |  |  |  |  |  |  |  |  |  |  |  |  |  |  |  |  |  |  |  1 wades_idler_block.stl
  |  |  |  | 1|  |  |  |  |  |  |  |  |  |  |  |  |  |  |  |  |  |  1 wades_small_gear.stl
  |  |  |  |  |  |  |  |  |  |  |  | 1|  |  |  |  |  |  |  |  |  |  1 x_belt_clamp.stl
  |  |  |  |  |  |  |  |  |  |  |  | 1|  |  |  |  |  |  |  |  |  |  1 x_belt_grip.stl
  |  |  |  |  |  |  |  |  |  |  |  | 1|  |  |  |  |  |  |  |  |  |  1 x_belt_tensioner.stl
  |  |  |  |  |  |  |  |  |  |  |  | 1|  |  |  |  |  |  |  |  |  |  1 x_carriage.stl
  |  |  |  |  |  |  |  |  |  |  |  |  | 1|  |  |  |  |  |  |  |  |  1 x_carriage_fan_bracket.stl
  |  |  |  |  |  |  |  |  |  |  |  |  | 1|  |  |  |  |  |  |  |  |  1 x_carriage_fan_duct.stl
  |  |  |  |  |  |  |  |  |  |  |  |  |  | 2| 2|  |  |  |  |  |  |  4 x_end_clamp.stl
  |  |  |  |  |  |  |  |  |  |  |  |  |  | 1|  |  |  |  |  |  |  |  1 x_idler_bracket.stl
  |  |  |  |  |  |  |  |  |  |  |  |  |  |  | 1|  |  |  |  |  |  |  1 x_motor_bracket.stl
  |  |  |  |  |  |  |  |  |  |  |  |  |  |  | 1|  |  |  |  |  |  |  1 x_motor_ribbon_bracket.stl
  |  |  |  |  |  |  |  |  |  |  |  |  |  |  |  | 3|  |  |  |  |  |  3 y_bar_clamp.stl
  |  |  |  |  |  |  |  |  |  |  |  |  |  |  |  | 1|  |  |  |  |  |  1 y_bar_clamp_switch.stl
  |  |  |  |  |  |  |  |  |  |  |  |  |  |  |  |  | 3|  |  |  |  |  3 y_bearing_mount.stl
  |  |  |  |  |  |  |  |  |  |  |  |  |  |  |  |  | 1|  |  |  |  |  1 y_belt_anchor.stl
  |  |  |  |  |  |  |  |  |  |  |  |  |  |  |  |  | 1|  |  |  |  |  1 y_belt_anchor_toothed.stl
  |  |  |  |  |  |  |  |  |  |  |  |  |  |  |  |  | 1|  |  |  |  |  1 y_belt_clip.stl
  |  |  |  |  |  |  |  |  |  |  |  |  |  |  |  |  | 1|  |  |  |  |  1 y_belt_clip_toothed.stl
  |  |  |  |  |  |  |  |  |  |  |  |  |  |  |  |  |  | 1|  |  |  |  1 y_idler_bracket.stl
  |  |  |  |  |  |  |  |  |  |  |  |  |  |  |  |  |  |  | 1|  |  |  1 y_motor_bracket.stl
  |  |  |  |  |  |  |  |  |  |  |  |  |  |  |  |  |  |  |  | 2|  |  2 z_bar_clamp.stl
  |  |  |  |  |  |  |  |  |  |  |  |  |  |  |  |  |  |  |  |  | 4|  4 z_coupling.stl
  |  |  |  |  |  |  |  |  |  |  |  |  |  |  |  |  |  |  |  |  | 1|  1 z_motor_bracket_lhs.stl
  |  |  |  |  |  |  |  |  |  |  |  |  |  |  |  |  |  |  |  |  | 1|  1 z_motor_bracket_rhs.stl
  |  |  |  |  |  |  |  |  |  |  |  |  |  |  |  |  |  |  |  | 2|  |  2 z_screw_pointer.stl

Sub-assemblies:
  1 bed_fan_assembly
  1 electronics_assembly
  1 extruder_assembly
  1 extruder_connection_pcb_assembly
  1 extruder_motor_assembly
  1 frame_assembly
  1 hot_end_assembly
  1 machine_assembly
  1 print_bed_assembly
  1 psu_assembly
  1 spool_holder_assembly
  1 x_axis_assembly
  1 x_carriage_assembly
  1 x_carriage_fan_assembly
  1 x_idler_assembly
  1 x_motor_assembly
  1 y_axis_assembly
  1 y_carriage_assembly
  1 y_idler_assembly
  1 y_motor_assembly
  1 z_axis_assembly
  2 z_motor_assemblies

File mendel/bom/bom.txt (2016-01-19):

Vitamins:
          E                                                      
          x                                                      
          t                                                      
          r                                                      
          u                                                      
          d                                                      
          e                                                      
          r                                                      
                                                                 
          c  E                          X                        
          o  x                                                   
          n  t                 S        c                        
    E     n  r                 p        a                        
    l     e  u                 o     X  r           Y            
    e     c  d           P     o        r                        
    c  E  t  e           r     l     c  i           c            
 B  t  x  i  r     H  M  i           a  a  X  X     a  Y  Y     Z
 e  r  t  o        o  a  n     h  X  r  g        Y  r        Z   
 d  o  r  n  m  F  t  c  t     o     r  e  i  m     r  i  m     m
    n  u     o  r     h        l  a  i     d  o  a  i  d  o  a  o
 f  i  d  p  t  a  e  i  b  P  d  x  a  f  l  t  x  a  l  t  x  t
 a  c  e  c  o  m  n  n  e  s  e  i  g  a  e  o  i  g  e  o  i  o
 n  s  r  b  r  e  d  e  d  u  r  s  e  n  r  r  s  e  r  r  s  r
  |  |  |  |  | 1|  |  |  |  |  |  |  |  |  |  |  |  |  |  |  |  |  1 Acrylic sheet 471mm x 422mm x 10mm
  |  |  |  |  | 2|  |  |  |  |  |  |  |  |  |  |  |  |  |  |  |  |  2 Acrylic sheet 165mm x 389mm x 6mm
  |  |  |  |  |  |  |  |  |  |  |  |  |  |  |  |  | 1|  |  |  |  |  1 Acrylic sheet 217mm x 217mm x 6mm
  |  |  |  |  | 1|  |  |  |  |  |  |  |  |  |  |  |  |  |  |  |  |  1 Acrylic sheet 471mm x 389mm x 6mm
  |  |  |  |  |  |  |  |  | 1|  |  |  |  |  |  |  |  |  |  |  |  |  1 THS15 Aluminium clad resistor 10R
  |  |  |  |  |  |  |  |  | 1|  |  |  |  |  |  |  |  |  |  |  |  |  1 THS15 Aluminium clad resistor 4R7
  |  |  |  |  |  |  |  |  | 1|  |  |  |  |  |  |  |  |  |  |  |  |  1 PSU e.g. ALPINE500
  |  | 3|  |  |  |  |  |  |  | 4|  |  |  |  |  |  |  |  |  |  |  |  7 Ball bearing 608 8mm x 22mm x 7mm
  |  |  |  |  |  |  |  |  |  |  |  |  |  | 2|  |  |  | 2|  |  |  |  4 Ball bearing 624 4mm x 13mm x 5mm
  |  |  |  |  |  |  |  | 4|  |  |  |  |  |  |  |  |  |  |  |  |  |  4 19mm bulldog clip
  |  |  |  |  |  |  |  | 1|  |  |  |  |  |  |  |  |  |  |  |  |  |  1 PCB bed 214mm x 214mm
  |  |  |  |  |  |  |  |  |  |  |  |  |  |  |  | 1|  |  |  |  |  |  1 Belt T2 x 6mm x 654mm
  |  |  |  |  |  |  |  |  |  |  | 1|  |  |  |  |  |  |  |  |  |  |  1 Belt T2 x 6mm x 868mm
  |  |  |  |  |  |  |  | 4|  |  |  |  |  |  |  |  |  |  |  |  |  |  4 Corrugated cardboard 201mm x 217mm x 5mm
  |  |  |  |  |  |  |  | 4|  |  |  |  |  |  |  |  |  |  |  |  |  |  4 M3 cap screw x 10mm
  | 4|  |  |  |  |  |  |  |  |  |  |  |  |  |  |  |  |  |  |  |  |  4 M3 cap screw x 12mm
  |  | 3|  |  |  |  |  |  |  |  |  | 2|  |  | 6| 4|14|  |  | 2| 2| 33 M3 cap screw x 16mm
  |  |  |  |  |  |  |  |  |  |  |  | 1|  | 8|10|  | 2|  |  |  | 8| 29 M3 cap screw x 20mm
  |  |  |  |  |  |  |  |  |  |  |  | 2|  |  |  |  |  |  |  |  |  |  2 M3 cap screw x 25mm
  |  |  |  | 2|  |  |  |  |  |  |  |  |  |  | 2|  |  |  |  |  |  |  4 M3 cap screw x 45mm
 4|  |  |  |  |  |  |  |  |  |  |  |  |  |  |  |  |  |  |  |  |  |  4 M4 cap screw x 20mm
  |  |  |  |  |  |  |  |  |  |  |  |  | 4|  |  |  |  | 1|  |  |  |  5 M4 cap screw x 30mm
  |  |  |  |  |  |  |  |  |  |  |  |  |  | 1|  |  |  |  |  |  |  |  1 M4 cap screw x 45mm
  |  |  |  |  |  |  |  |  |  | 4|  |  |  |  |  |  |  |  |  |  |  |  4 M8 cap screw x 30mm
  |  |  | 1|  |  |  |  |  |  |  |  |  |  |  |  |  |  |  |  |  |  |  1 15 way D PCB mount plug
  |  |  |  |  |  |  |  |  |  |  |  |  |  |  | 1|  |  |  |  |  |  |  1 15 way D IDC socket
  |  |  |  |  |  |  |  |  |  |  |  |  | 1|  |  |  |  |  |  |  |  |  1 Fan 60mm x 15mm
  |  |  |  |  |  |  |  |  |  | 1|  |  |  |  |  |  |  |  |  |  |  |  1 Foam sponge 20mm x 20mm x 20mm
  |  |  |  | 1|  |  |  |  |  |  |  |  |  |  | 2|  |  |  | 2|  |  |  5 M3 grub screw x 6mm
  |  |  |  |  |  |  |  | 1|  |  |  |  |  |  |  |  |  |  |  |  |  |  1 Glass sheet 214mm x 202mm x 2mm
  |  |  |  |  |  | 1|  |  |  |  |  |  |  |  |  |  |  |  |  |  |  |  1 JHead MK5 hot end 3mm
  |  |  |  |  |  |  |  | 4|  |  |  |  |  |  |  |  |  |  |  |  |  |  4 Hex male / female pillar M3 x 20mm
  |  | 3|  |  |  |  |  |  |  |  |  |  |  |  |  |  |  |  |  |  |  |  3 M3 hex screw x 10mm
  |  | 2|  |  |  |  |  |  |  |  |  |  |  |  |  |  |  |  |  |  |  |  2 M4 hex screw x 20mm
  |  | 2|  |  |  |  |  |  |  |  |  |  |  |  |  |  |  |  |  |  |  |  2 M4 hex screw x 50mm
  |  | 1|  |  |  |  |  |  |  |  |  |  |  |  |  |  |  |  |  |  |  |  1 M8 hex screw x 60mm, hobbed at 25
  |  |  |  |  |  |  |  |  | 1|  |  |  |  |  |  |  |  |  |  |  |  |  1 IEC mains lead
  |  |  |  |  |  |  |  |  |  |  |  | 3|  | 2| 2|  | 3|  |  |  |  | 10 LM8UU linear bearing
  | 1|  |  |  |  |  |  |  |  |  |  |  |  |  |  |  |  |  |  |  |  |  1 Melzi electronics
  |  |  | 1|  |  |  |  |  |  |  |  |  |  |  |  |  |  |  |  |  |  |  1 2 way Molex KK header
  |  |  | 1|  |  |  |  |  |  |  |  |  |  |  |  |  |  |  |  |  |  |  1 3 way Molex KK header
  |  |  |  | 1|  |  |  |  |  |  |  |  |  |  | 1|  |  |  | 1|  | 2|  5 NEMA17 x 47mm stepper motor
  |  |  |  |  |  |  |  |  |  |  |  |  |  |  |  |  |  |  |  | 2|  |  2 Brass nut M8
  |  | 3|  | 3|  |  |  |  |  |  |  | 1|  |  |  |  |  |  |  |  |  |  7 Nut M3
  |  | 2|  |  |  |  |  |  |  |  |  |  |  |  |  |  |  |  |  |  |  |  2 Nut M4
  |  | 2|  |  |  |  |  |  |  |  |  |  |  |  |  |  |  |  |  |  |  |  2 Nut M8
  |  |  |  |  |  |  |  |  |  |  |  | 4|  | 8|14| 4|16|  |  | 2|10| 58 Nyloc nut M3
 4|  |  |  |  |  |  |  |  |  |  |  |  | 4| 1|  |  |  | 1|  |  |  | 10 Nyloc nut M4
  |  |  |  |  |  |  |  |  |  | 4|  |  |  |  |  |  |  |  |  |  |  |  4 Nyloc nut M8
  |  |  |  |  |  |  |  |  |  |  |  |  |  |  | 2|  |  |  |  |  |  |  2 Nitrile O-ring 2.5mm x 1.6mm
  |  |  | 1|  |  |  |  |  |  |  |  |  |  |  |  |  |  |  |  |  |  |  1 Extruder connection PCB
  |  |  |  |  |  |  |  |  |  | 1|  |  |  |  |  |  |  |  |  |  |  |  1 PLA sample 3mm ~50m
  |  |  |  |  |  |  |  |  |  |  |  |  |  |  | 1|  |  |  |  |  |  |  1 Polypropylene strip 395mm x 18mm x 0.5mm
  |  |  |  |  |  |  |  |  |  |  |  |  |  |  | 1|  |  |  |  |  |  |  1 Polypropylene strip 475mm x 25mm x 0.5mm
  |  |  |  |  |  |  |  | 1|  |  |  |  |  |  |  |  |  |  |  |  |  |  1 Polypropylene strip 271mm x 33mm x 0.5mm
  |  |  |  |  |  |  |  |  | 4|  |  |  |  |  |  |  |  |  |  |  |  |  4 M2.5 pan screw x 12mm
  |  |  |  |  |  |  |  |  |  |  |  |  |  |  | 2|  |  |  | 4|  | 8| 14 M3 pan screw x 8mm
  |  |  |  |  |28|  |  |  | 4| 2|  |  |  |  |  |  |  |  |  | 4| 4| 42 M4 pan screw x 12mm
  |  |  |  |  |11|  |  |  |  |  |  |  |  |  |  | 8|  | 1| 4|  |  | 24 M4 pan screw x 16mm
  |  |  |  |  |  |  |  |  | 2|  |  |  |  |  |  |  |  |  |  |  |  |  2 6-32 pan screw x 9.5mm
  |  |  |  | 2|  |  |  |  |  |  |  |  |  |  | 4| 2|  |  |  | 2|  | 10 No2 pan wood screw x 13mm
  |  |  |  |  |  |  |  |  |  |  |  |  |  |  | 1|  |  |  | 1|  |  |  2 GT2 pulley 20 teeth
  |  |  |  |  |  |  |  |  |  |  |  |  |  |  | 1|  |  |  |  |  |  |  1 Ribbon cable 20 way 1240mm
  |  |  |  |  |  |  |  | 1|  |  |  |  |  |  |  |  |  |  |  |  |  |  1 Ribbon cable 26 way 381mm
  |  | 1|  |  |  |  |  |  |  |  |  |  |  |  |  |  |  |  |  |  |  |  1 Smooth rod 8mm x 22mm
  |  |  |  |  |  |  |  |  |  |  |  |  |  |  |  | 1|  |  |  |  |  |  1 Smooth rod 8mm x 271mm
  |  |  |  |  |  |  |  |  |  |  |  |  |  |  |  |  |  |  |  | 2|  |  2 Smooth rod 8mm x 340mm
  |  |  |  |  |  |  |  |  |  |  | 2|  |  |  |  |  |  |  |  |  |  |  2 Smooth rod 8mm x 385mm
  |  |  |  |  |  |  |  |  |  |  |  |  |  |  |  | 1|  |  |  |  |  |  1 Smooth rod 8mm x 418mm
  | 1|  |  |  |  |  |  |  |  |  |  |  |  |  |  |  |  |  |  |  |  |  1 Micro SD card
  | 1|  |  |  |  |  |  |  |  |  |  |  |  |  |  |  |  |  |  |  |  |  1 Micro SD to USB adapter
  |  |  |  |  |  |  |  |  |  |  |  |  |  |  | 1| 1|  |  |  | 1|  |  3 Microswitch
  |  | 2|  |  |  |  |  |  |  |  |  |  |  |  |  |  |  |  |  |  |  |  2 Spring 7mm OD, 1mm gauge x 10mm long
  |  |  |  |  |  | 1|  |  |  |  |  |  |  |  |  |  |  |  |  |  |  |  1 110mm x 25mm self amalgamating silicone tape
  |  |  |  |  |  |  |  |  |  |  |  |  |  |  |  |  |  |  |  | 2|  |  2 Threaded rod M8 x 300mm
  |  |  |  |  |  |  |  |  | 1|  |  |  |  |  |  |  |  |  |  |  |  |  1 Heatshrink sleeving ID 10mm x 15mm
  |  |  |  |  |  | 2|  |  |  |  |  |  |  |  |  |  |  |  |  |  |  |  2 PTFE sleeving OD 1.2mm ID 0.71mm x 62mm
  |  |  |  |  |  | 2|  | 2|  |  |  |  |  |  |  |  |  |  |  |  |  |  4 Heatshrink sleeving ID 1.6mm x 15mm
  |  |  |  |  |  | 2|  |  |  |  |  |  |  |  |  |  |  |  |  |  |  |  2 PTFE sleeving OD 2.6mm ID 2mm x 45mm
  | 2|  |  |  |  |  |  | 2| 3|  |  |  |  |  | 4|  |  |  |  |  |  | 11 Heatshrink sleeving ID 2.4mm x 15mm
  |  |  |  |  |  |  |  |  | 5|  |  |  |  |  |  |  |  |  |  |  |  |  5 Heatshrink sleeving ID 3.2mm x 15mm
  |  |  |  |  |  |  |  |  |  | 1|  |  |  |  |  |  |  |  |  |  |  |  1 PTFE tubing OD 4.6mm ID 3.84mm x 750mm
  |  |  |  |  |  |  |  |  | 2|  |  |  |  |  |  |  |  |  |  |  |  |  2 Heatshrink sleeving ID 6.4mm x 15mm
  |  |  |  |  |  |  |  | 2|  |  |  |  |  |  |  |  |  |  |  |  |  |  2 Heatshrink sleeving ID 6.4mm x 30mm
  |  |  |  |  |  | 1|  |  |  |  |  |  |  |  |  |  |  |  |  |  |  |  1 Heatshrink sleeving ID 6.4mm x 60mm
  |  |  |  |  |  |  |  |  |  |  |  |  |  |  |  |  |  |  |  |  | 2|  2 Neoprene tubing OD 8mm ID 5mm x 16mm
  |  |  | 2|  |  |  |  |  |  |  |  |  |  |  |  |  |  |  |  |  |  |  2 4 way terminal block
  |  |  |  |  |  |  |  | 1|  |  |  |  |  |  |  |  |  |  |  |  |  |  1 Epcos B57861S104F40 100K 1% thermistor
  | 1|  |  |  |  |  |  |  |  |  |  |  |  |  |  |  |  |  |  |  |  |  1 USB A to Mini B lead
  |  |  |  | 2|  |  |  |  |  |  |  |  |  |  | 4| 2|  |  |  | 2|  | 10 Washer M2.5 x 5.9mm x 0.5mm
  | 4| 3|  | 2|  |  |  | 4|  |  |  | 4|  | 8|22| 4|22|  | 4| 2|18| 97 Washer M3 x 7mm x 0.5mm
 4|  | 7|  |  |39|  |  |  | 6| 2|  |  | 4| 2|  | 8|  | 5| 4| 4| 4| 89 Washer M4 x 9mm x 0.8mm
  |  |  |  |  |  |  |  |  |  |  |  |  |  | 2|  |  |  | 2|  |  |  |  4 Washer M5 x 20mm x 1.4mm
  |  |  |  |  |  |  |  |  |  |12|  |  |  |  |  |  |  |  |  |  |  | 12 Washer M8 x 17mm x 1.6mm
  |  |  |  |  |  |  |  |  |  | 4|  |  |  |  |  |  |  |  |  |  |  |  4 Washer M8 x 30mm x 1.5mm
  |  |  |  |  |  |  |  |  |  |  | 2|  |  |  |  |  |  |  |  |  |  |  2 Wingnut M4
  |  |  |  |  |  | 2|  |  |  |  |  |  |  |  |  |  |  |  |  |  |  |  2 Red PTFE wire 16/0.2 length 170mm
  |  |  |  |  |  |  |  | 1|  |  |  |  |  |  |  |  |  |  |  |  |  |  1 Black wire 32/0.2 length 635mm
  |  |  |  |  |  |  |  | 1|  |  |  |  |  |  |  |  |  |  |  |  |  |  1 Red wire 32/0.2 length 620mm
  | 4| 6|  |  |  |  |  |  |  |  |  |  |  |  | 2|  |  |  | 4|  | 8| 24 Star washer M3 x 0.5mm
  |  |  |  |  |39|  |  |  | 6| 2|  |  |  |  |  | 8|  | 1| 4| 4| 4| 68 Star washer M4 x 0.8mm
  |  | 1|  |  |  |  |  |  |  |  |  |  |  |  |  |  |  |  |  |  |  |  1 Star washer M8 x 1.6mm
  |  |  |  |  |  | 1|  |  | 2|  |  | 3|  |  |  |  | 3|  |  |  |  |  9 Ziptie 100mm min length
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

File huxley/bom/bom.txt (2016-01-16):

Vitamins:
          E                                                      
          x                                                      
          t                                                      
          r                                                      
          u                                                      
          d                                                      
          e                                                      
          r                                                      
                                                                 
          c  E                          X                        
          o  x                                                   
          n  t                 S        c                        
    E     n  r                 p        a                        
    l     e  u                 o     X  r           Y            
    e     c  d           P     o        r                        
    c  E  t  e           r     l     c  i           c            
 B  t  x  i  r     H  M  i           a  a  X  X     a  Y  Y     Z
 e  r  t  o        o  a  n     h  X  r  g        Y  r        Z   
 d  o  r  n  m  F  t  c  t     o     r  e  i  m     r  i  m     m
    n  u     o  r     h        l  a  i     d  o  a  i  d  o  a  o
 f  i  d  p  t  a  e  i  b  P  d  x  a  f  l  t  x  a  l  t  x  t
 a  c  e  c  o  m  n  n  e  s  e  i  g  a  e  o  i  g  e  o  i  o
 n  s  r  b  r  e  d  e  d  u  r  s  e  n  r  r  s  e  r  r  s  r
  |  |  |  |  |  |  |  |  |  | 4|  |  |  |  |  |  |  |  |  |  |  |  4 Ball bearing 608 8mm x 22mm x 7mm
  |  | 1|  |  |  |  |  |  |  |  |  |  |  | 2|  |  |  | 2|  |  |  |  5 Ball bearing 624 4mm x 13mm x 5mm
  |  |  |  |  |  |  |  | 4|  |  |  |  |  |  |  |  |  |  |  |  |  |  4 19mm bulldog clip
  |  |  |  |  |  |  |  | 1|  |  |  |  |  |  |  |  |  |  |  |  |  |  1 PCB bed 165mm x 160mm
  |  |  |  |  |  |  |  |  |  |  |  |  |  |  |  | 1|  |  |  |  |  |  1 Belt T2 x 6mm x 512mm
  |  |  |  |  |  |  |  |  |  |  | 1|  |  |  |  |  |  |  |  |  |  |  1 Belt T2 x 6mm x 690mm
  |  |  |  |  |  |  |  | 4|  |  |  |  |  |  |  |  |  |  |  |  |  |  4 Corrugated cardboard 149mm x 159mm x 5mm
  |  |  |  |  | 2|  |  | 4|  |  |  |  |  |  |  |  |  |  |  |  |  |  6 M3 cap screw x 10mm
  | 4| 4|  |  |34|  |  |  |  | 2|  | 2|  | 8|12|12|14| 1| 4| 6|14|117 M3 cap screw x 16mm
  |  |  |  |  |  |  |  |  |  |  |  | 1|  |  | 2|  | 2|  |  |  |  |  5 M3 cap screw x 20mm
  |  | 1|  |  |  |  |  |  |  |  |  | 2| 4|  |  |  |  |  |  |  |  |  7 M3 cap screw x 25mm
  |  |  |  | 2|  |  |  |  |  |  |  |  |  |  | 2|  |  |  |  |  |  |  4 M3 cap screw x 35mm
 4|  |  |  |  |  |  |  |  |  |  |  |  |  |  |  |  |  |  |  |  |  |  4 M4 cap screw x 16mm
  |  |  |  |  |  |  |  |  |  |  |  |  |  |  |  |  |  | 1|  |  |  |  1 M4 cap screw x 30mm
  |  | 1|  |  |  |  |  |  |  |  |  |  |  |  |  |  |  |  |  |  |  |  1 M4 cap screw x 35mm
  |  |  |  |  |  |  |  |  |  |  |  |  |  | 1|  |  |  |  |  |  |  |  1 M4 cap screw x 45mm
  |  |  |  |  |  |  |  |  |  | 4|  |  |  |  |  |  |  |  |  |  |  |  4 M8 cap screw x 30mm
  |  |  |  |  | 2|  |  |  |  |  |  |  |  |  |  |  |  |  |  |  |  |  2 Dibond sheet 122mm x 317mm x 3mm
  |  |  |  |  |  |  |  |  |  |  |  |  |  |  |  |  | 1|  |  |  |  |  1 Dibond sheet 164mm x 159mm x 3mm
  |  |  |  |  | 1|  |  |  |  |  |  |  |  |  |  |  |  |  |  |  |  |  1 Dibond sheet 356mm x 313mm x 3mm
  |  |  |  |  | 1|  |  |  |  |  |  |  |  |  |  |  |  |  |  |  |  |  1 Dibond sheet 356mm x 317mm x 3mm
  |  |  | 1|  |  |  |  |  |  |  |  |  |  |  |  |  |  |  |  |  |  |  1 15 way D PCB mount plug
  |  |  |  |  |  |  |  |  |  |  |  |  |  |  | 1|  |  |  |  |  |  |  1 15 way D IDC socket
  |  |  |  |  |  |  |  |  |  |  |  |  | 1|  |  |  |  |  |  |  |  |  1 Fan 40mm x 11mm
 1|  |  |  |  |  |  |  |  |  |  |  |  |  |  |  |  |  |  |  |  |  |  1 Fan 80mm x 25mm
  |  |  |  |  |  |  |  |  |  | 1|  |  |  |  |  |  |  |  |  |  |  |  1 Foam sponge 20mm x 20mm x 20mm
  |  |  |  | 1|  |  |  |  |  |  |  |  |  |  |  |  |  |  |  |  |  |  1 M3 grub screw x 3mm
  |  |  |  |  |  |  |  |  |  |  |  |  |  |  | 2|  |  |  | 2|  |  |  4 M3 grub screw x 6mm
  |  |  |  |  |  |  |  | 1|  |  |  |  |  |  |  |  |  |  |  |  |  |  1 Glass sheet 150mm x 160mm x 2mm
  |  |  |  |  |  | 1|  |  |  |  |  |  |  |  |  |  |  |  |  |  |  |  1 JHead MK5 hot end 1.75mm
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

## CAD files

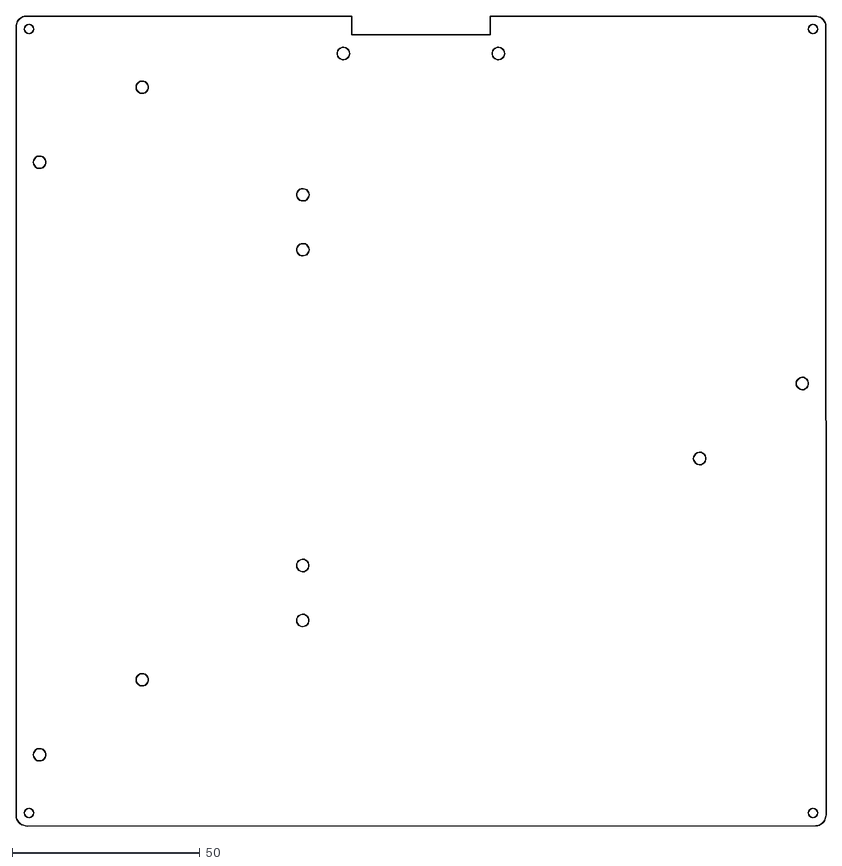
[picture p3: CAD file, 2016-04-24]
dibond/sheets/y_carriage.dxf
216.0 x 216.0

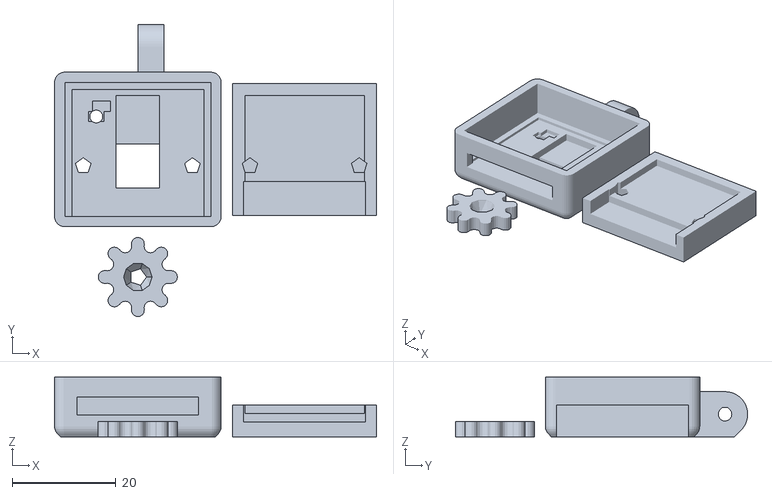
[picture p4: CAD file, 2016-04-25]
dibond/stls/accessories/rpi_camera_case.stl
61.9 x 56.2 x 11.5

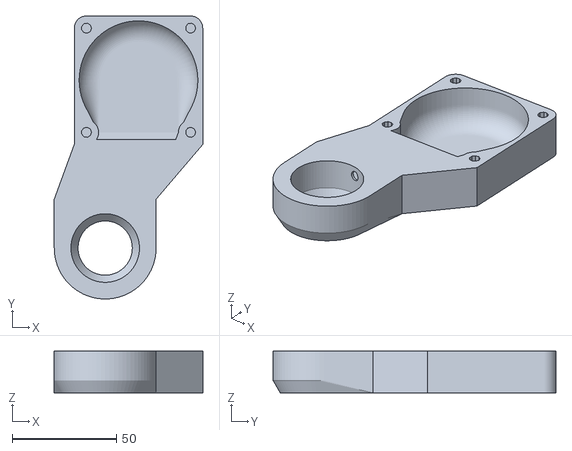
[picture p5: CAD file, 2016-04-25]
dibond/stls/printed/x_carriage_fan_duct.stl
71.3 x 135.9 x 20.0

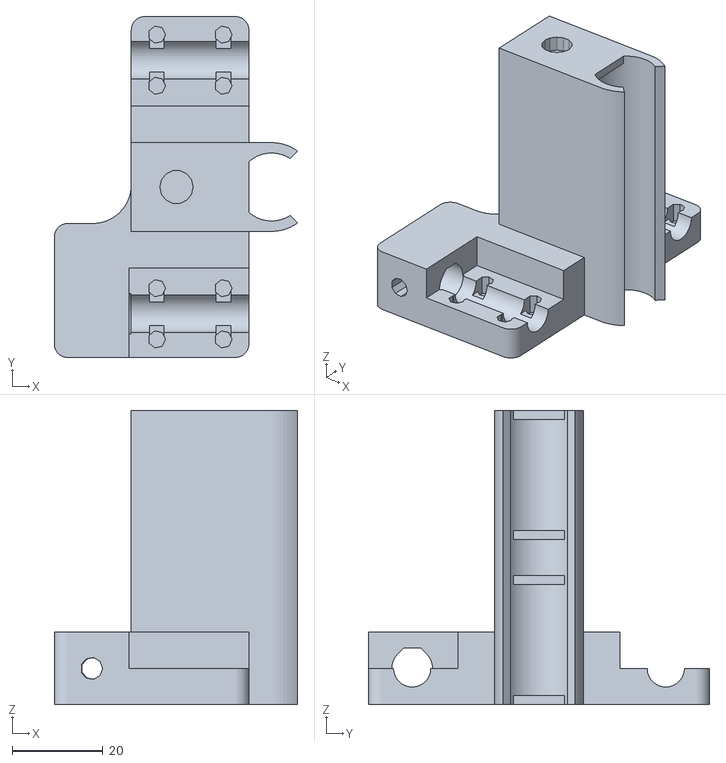
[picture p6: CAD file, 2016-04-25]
dibond/stls/x_idler_bracket.stl
53.8 x 75.3 x 65.0

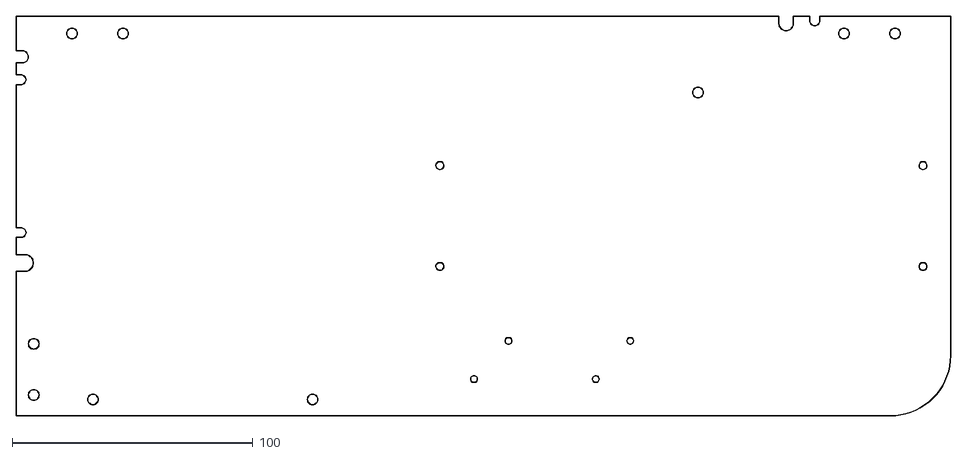
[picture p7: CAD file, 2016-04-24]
dibond_E3D/sheets/frame_right.dxf
388.0 x 166.0

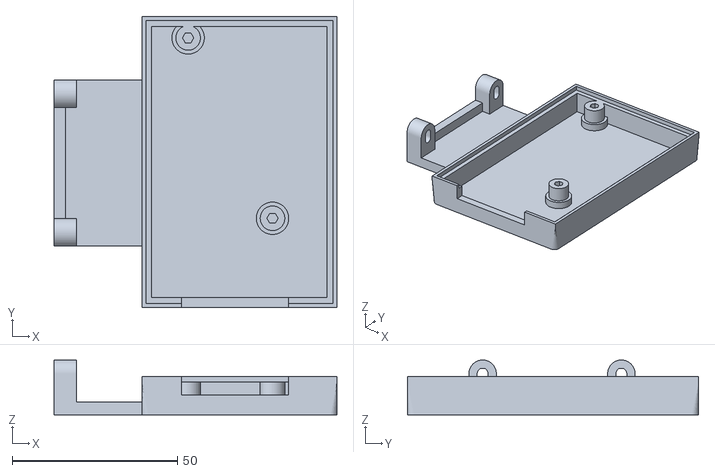
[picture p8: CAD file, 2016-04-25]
dibond_E3D/stls/accessories/rpi_bracket.stl
85.5 x 87.9 x 16.6

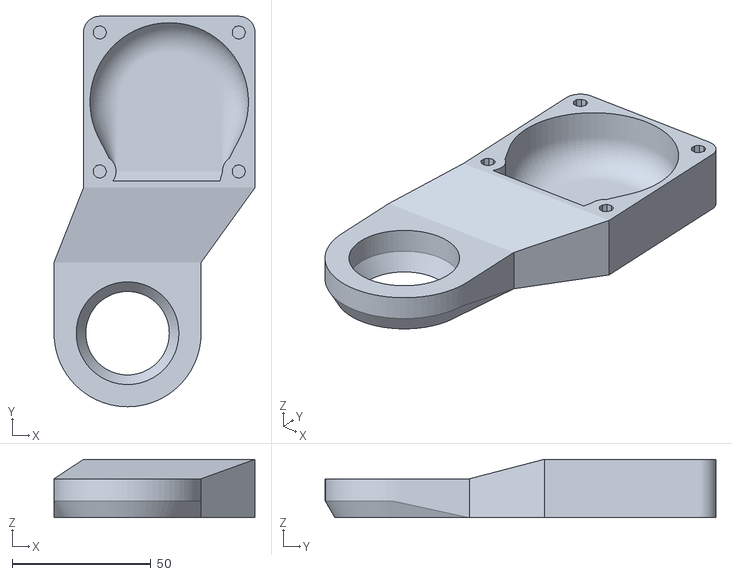
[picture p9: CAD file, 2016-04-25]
dibond_E3D/stls/printed/x_carriage_fan_duct.stl
72.3 x 140.5 x 21.0

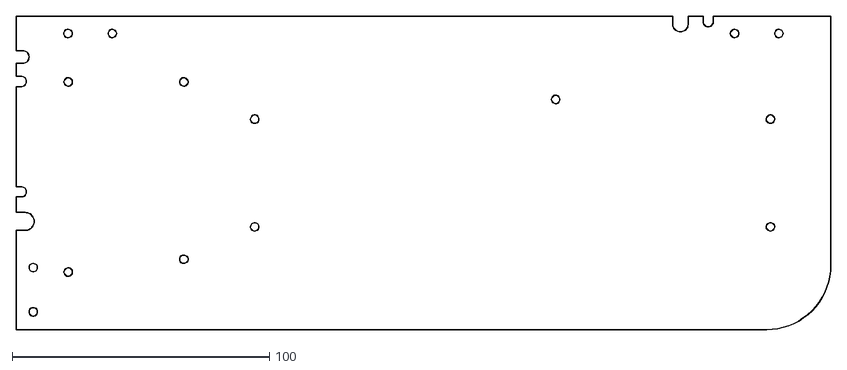
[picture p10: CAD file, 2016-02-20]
huxley/sheets/frame_right.dxf
317.0 x 121.9

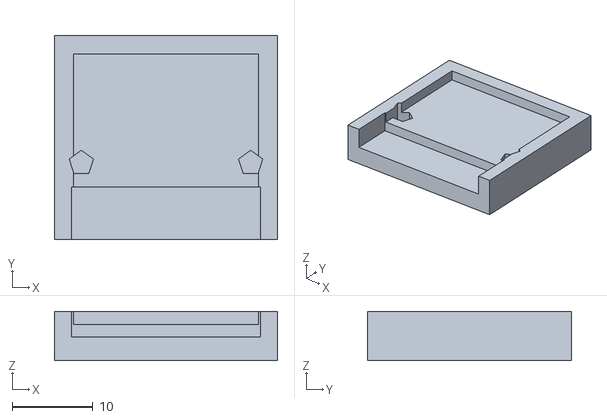
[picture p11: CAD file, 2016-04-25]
huxley/stls/accessories/rpi_camera_back.stl
27.7 x 25.3 x 6.10

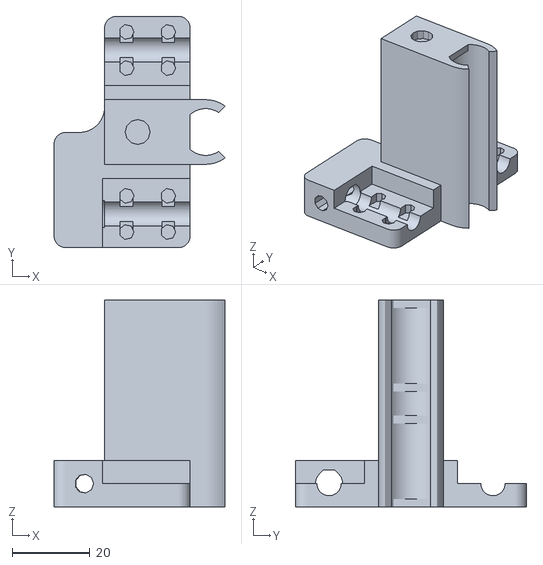
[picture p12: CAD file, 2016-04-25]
huxley/stls/printed/x_idler_bracket.stl
43.9 x 59.4 x 53.2

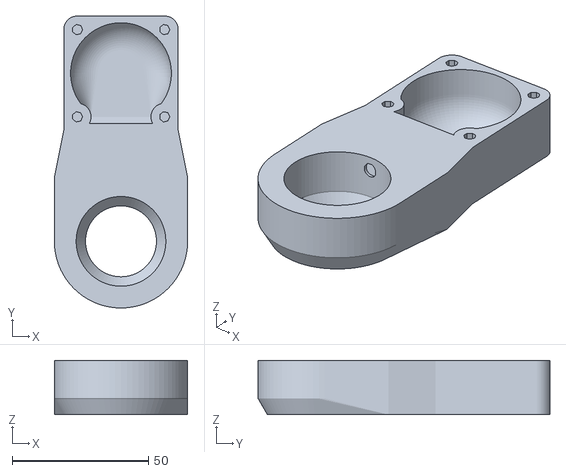
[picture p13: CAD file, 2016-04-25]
huxley/stls/x_carriage_fan_duct.stl
48.9 x 107.2 x 20.0

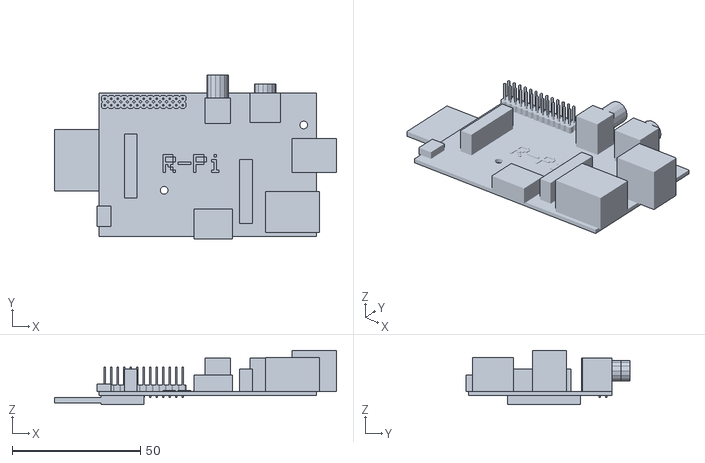
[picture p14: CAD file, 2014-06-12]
imported_stls/R-Pi.stl
110.1 x 64.0 x 21.2

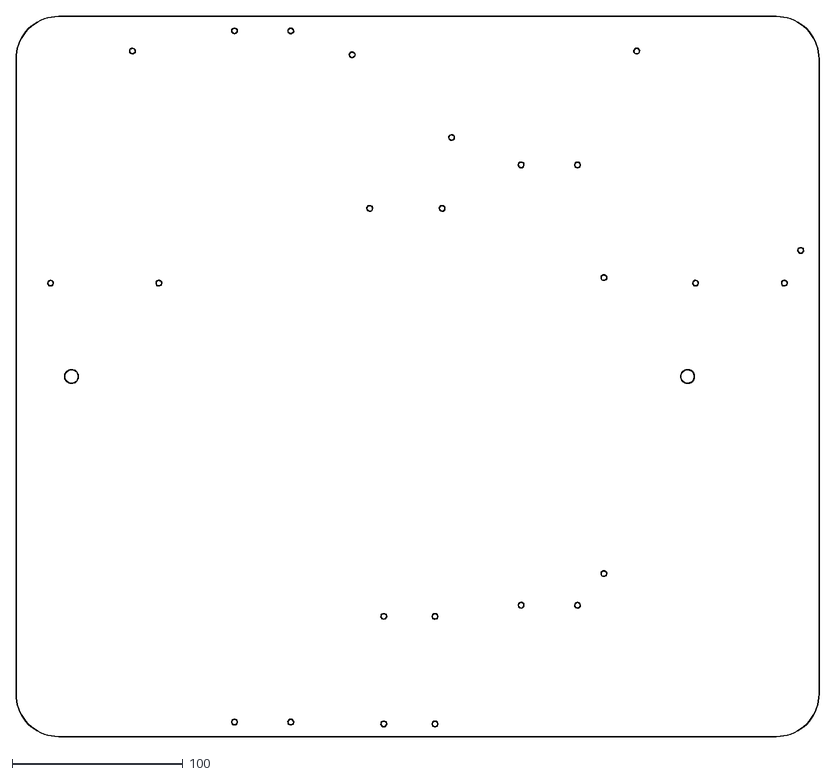
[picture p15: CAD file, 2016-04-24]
mendel/sheets/frame_base.dxf
470.5 x 422.0

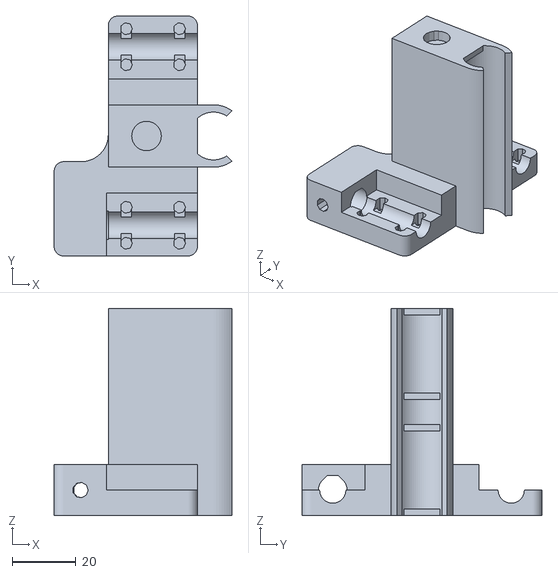
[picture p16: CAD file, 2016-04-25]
mendel/stls/printed/x_idler_bracket.stl
55.8 x 75.3 x 65.0

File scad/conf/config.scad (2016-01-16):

//
// Mendel90
//
// GNU GPL v2
// nop.head@gmail.com
// hydraraptor.blogspot.com
//
// Configuration file
//
bom = $bom == undef ? 0: $bom;                 // 0 no bom, 1 assemblies and stls, 2 vitamins as well
exploded = $exploded == undef ? 0 : $exploded; // 1 for exploded view

show_jigs = true;               // show printed jigs required to build the machine
show_support = true;            // show support structures, must be set when generating STLs
show_rays = false;              // show light and camera rays to check orientation is correct

// Real-world colors for various parts & vitamins
use_realistic_colors = false;    // true for "real" colors, false for "distinct" colors (useful during design and for build instructions)
printed_plastic_color = "blue";
cable_strip_real_color = "fuchsia";
belt_real_color = "yellow";
bulldog_real_color ="black";

eta = 0.01;                     // small fudge factor to stop CSG barfing on coincident faces.
$fa = 5;
$fs = 0.5;

function sqr(x) = x * x;            // shortcut

module rotate(a)
{
 cx = cos(a[0]);
 cy = cos(a[1]);
 cz = cos(a[2]);
 sx = sin(a[0]);
 sy = sin(a[1]);
 sz = sin(a[2]);
 multmatrix([
  [ cy * cz, cz * sx * sy - cx * sz, cx * cz * sy + sx * sz, 0],
  [ cy * sz, cx * cz + sx * sy * sz,-cz * sx + cx * sy * sz, 0],
  [-sy,      cy * sx,                cx * cy,                0],
  [ 0,       0,                      0,                      1]
 ]) children();
}

cnc_tool_dia = 2.4;
layer_height = 0.4;
filament_width = layer_height * 1.5;
min_wall = 2 * filament_width + eta;
part_base_thickness = 5;;           // The thickness of things screwed to the frame

pcb_thickness = 1.6;
feed_tube_rad = 5 / 2;              // Filament feed tube
feed_tube_tape_rad = 6.2 / 2;
feed_tube_tape = 12;
function nozzle_length(hot_end) = max(54, hot_end_length(hot_end));    // how far nozzle extends below top of carriage

include <colors.scad>
include <utils.scad>
include <vitamins.scad>

endstop_wires    = [2, 1.4, "A"];   // 7 strands of 0.2
motor_wires      = [4, 1.4, "B"];
bed_wires        = [2, 2.8, "C"];   // 13A mains cable
fan_motor_wires  = [6, 1.4, "D"];   // fan and motor wires along top of gantry
two_motor_wires  = [8, 1.4,,"E"];   // Y and Z motors
thermistor_wires = endstop_wires;

endstop_wires_hole_radius = wire_hole_radius(endstop_wires);
motor_wires_hole_radius = wire_hole_radius(motor_wires);
two_motor_wires_hole_radius = wire_hole_radius(two_motor_wires);
fan_motor_wires_hole_radius = wire_hole_radius(fan_motor_wires);
bed_wires_hole_radius = wire_hole_radius(bed_wires);
thermistor_wires_hole_radius = wire_hole_radius(thermistor_wires);

cnc_sheets = false;                 // If sheets are cut by CNC we can use slots, etc instead of just round holes
base_nuts = false;                  // Need something under the base if using nuts
pulley_type = T5x8_plastic_pulley;
clip_handles = true;
include_fan = false;
squeeze = false;                    // Bodge to make Huxley as small as possible without affecting dibond kits
part_fan = fan60x15;
extruder = Wades;                   // Default extruder
raspberry_pi = false;               // Raspberry pi mounted on PSU
raspberry_pi_camera = false;        // RPI camera on bar across the back
light_strip = false;
vero_bed = false;                   // Bed made from vero board rather than custom PCB.
include <machine.scad>              // this file is generated from the command line parameter to include one of the machine configs

screw_clearance_radius = screw_clearance_radius(cap_screw);
nut = screw_nut(cap_screw);
nut_radius = nut_radius(nut);
nut_trap_depth = nut_trap_depth(nut);
washer = screw_washer(cap_screw);

bearing_clamp_tab = cnc_sheets ? (nut_radius(nut) + 3 * filament_width) * 2 : washer_diameter(washer) + 2;   // how much the lugs stick out and their width
bearing_clamp_tab_height = 4;           // thickness of the lugs

hole_edge_clearance = 5;                // how close a hole can be to the edge of a sheet
base_clearance = cnc_sheets ? 1 : 2;    // how close we get to the edge of the base
axis_end_clearance = cnc_sheets ? 1 : 2;// how close we get to the end of an axis
limit_switch_offset = 1;                // the over travel to reach the limit switch
X_carriage_clearance = 2;               // how close the X carriage is to the XZ plane
                                        // how close the Y carriage is to the window in the XZ plane
Y_carriage_clearance = 2 + (clip_handles ? (bulldog_handle_length(small_bulldog) - (Y_carriage_width - bed_width) / 2) : 0);
Y_carriage_rad = 3;                     // corner radius
Z_clearance = 10;                       // How close the top of the object gets to the gantry
belt_clearance = 0.2;                   // clearance of belt clamp slots

X_bar_dia = bearing_rod_dia(X_bearings);      // rod sizes to match the bearings
Y_bar_dia = bearing_rod_dia(Y_bearings);
Z_bar_dia = bearing_rod_dia(Z_bearings);

Y_idler_bearing = BB624;
X_idler_bearing = BB624;

extruder_ways = 4 + 6 + 2 + 1 + 1;      // motor + heater(x3) + thermistor + probe + fan = 14
x_end_ways = extruder_ways + 4 + 2;     // motor plus limit switch = 20
bed_ways = 24 + 2;                      // twelve each way for the current plus a thermistor

module wire_hole_or_slot(r) {
    if(cnc_sheets)
        rotate([0, 0, 90])
            slot(r = r, h = 100, l = 2 * r);
    else
        translate([0, r + hole_edge_clearance, 0])
            wire_hole(r);
}

function z_bar_offset() = round(NEMA_width(Z_motor)) / 2;

base_screw = sheet_is_soft(base) ? frame_soft_screw : (base_nuts ? frame_thin_screw : frame_thick_screw);
base_nut = base_nuts ? screw_nut(base_screw) : false;
base_nut_traps = base_nuts && cnc_sheets;
base_washer = screw_washer(base_screw);
base_screw_length = base_nuts ? screw_longer_than(
                                    sheet_thickness(base)
                                    + part_base_thickness +
                                    (cnc_sheets ? 1 : 2) * washer_thickness(base_washer)
                                    + nut_thickness(base_nut, true)
                                  )
                              : screw_shorter_than(
                                    sheet_thickness(base)
                                    + part_base_thickness
                                    + 2 * washer_thickness(base_washer)
                                 );


frame_screw = sheet_is_soft(frame) ? frame_soft_screw : (frame_nuts ? frame_thin_screw : frame_thick_screw);
frame_nut = frame_nuts ? screw_nut(frame_screw) : false;
frame_nut_traps = frame_nuts && cnc_sheets;
frame_washer = screw_washer(frame_screw);
frame_screw_length = frame_nuts ? screw_longer_than(
                                      sheet_thickness(frame)
                                      + part_base_thickness +
                                      (cnc_sheets ? 1 : 2) * washer_thickness(frame_washer)
                                      + nut_thickness(frame_nut, true)
                                  )

                                : screw_shorter_than(
                                      sheet_thickness(frame)
                                      + part_base_thickness
                                      + 2 * washer_thickness(frame_washer)
                                  );

echo("base screw length", base_screw_length);
echo("frame screw length",frame_screw_length);



module frame_screw(thickness) {
    if(frame_nuts && cnc_sheets) {
        nut(frame_nut, true);
        translate([0, 0, -sheet_thickness(frame) - thickness])
            rotate([180, 0, 0])
                screw_and_washer(frame_screw, frame_screw_length);
    }
    else {
        screw_and_washer(frame_screw, frame_screw_length, !frame_nuts);
        if(frame_nuts)
            translate([0, 0, -sheet_thickness(frame) - thickness])
                rotate([180, 0, 0])
                    nut_and_washer(frame_nut, true);
    }
}

module frame_screw_hole() {
    cylinder(r = frame_nuts ? screw_clearance_radius(frame_screw) : screw_pilot_hole(frame_screw), h = 100, center = true);
}



module base_screw(thickness) {
    if(base_nuts && cnc_sheets) {
        nut(base_nut, true);
        translate([0, 0, -sheet_thickness(base) - thickness])
            rotate([180, 0, 0])
                screw_and_washer(base_screw, base_screw_length);
    }
    else {
        screw_and_washer(base_screw, base_screw_length, !base_nuts);
        if(base_nuts)
            translate([0, 0, -sheet_thickness(base) - thickness])
                rotate([180, 0, 0])
                    nut_and_washer(base_nut, true);
    }
}

module base_screw_hole() {
    cylinder(r = base_nuts ? screw_clearance_radius(base_screw) : screw_pilot_hole(base_screw), h = 100, center = true);
}
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

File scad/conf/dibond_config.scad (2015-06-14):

//
// Mendel90
//
// GNU GPL v2
// nop.head@gmail.com
// hydraraptor.blogspot.com
//
// Configuration file
//
echo("DiBond:");

Z_bearings = LM8UU;
Y_bearings = LM8UU;
X_bearings = LM8UU;

X_motor = NEMA17;
Y_motor = NEMA17;
Z_motor = NEMA17;

hot_end = JHeadMk5;

X_travel = 200;
Y_travel = 200;
Z_travel = 200;

bed_depth = 214;
bed_width = 214;
bed_pillars = M3x20_pillar;
bed_glass = glass2;
bed_thickness = pcb_thickness + sheet_thickness(bed_glass);    // PCB heater plus glass sheet
bed_holes = [209, 209];

base = DiBond;                  // Sheet material used for the base. Needs to be thick enough to screw into.
base_corners = 25;
base_nuts = true;

frame = DiBond;
frame_corners = 25;
frame_nuts = true;

case_fan = fan80x38;
psu = ALPINE500;
controller = Melzi;
spool = spool_300x85;
bottom_limit_switch = false;
top_limit_switch = true;

single_piece_frame = true;
stays_from_window = false;
cnc_sheets = true;                 // If sheets are cut by CNC we can use slots, etc instead of just round holes
//raspberry_pi = true;
//raspberry_pi_camera = true;
//light_strip = SPS125;

Y_carriage = DiBond;

pulley_type = GT2x20_metal_pulley;
X_belt = GT2x6;
Y_belt = GT2x6;

motor_shaft = 5;
Z_screw_dia = 6;            // Studding for Z axis

Y_carriage_depth = bed_holes[1] + 7;
Y_carriage_width = bed_holes[0] + 7;

Z_nut_radius = M6_nut_radius;
Z_nut_depth = M6_nut_depth;
Z_nut = M6_nut;

//
// Default screw use where size doesn't matter
//
cap_screw = M3_cap_screw;
hex_screw = M3_hex_screw;
//
// Screw for the frame and base
//
frame_soft_screw = No6_screw;               // Used when sheet material is soft, e.g. wood
frame_thin_screw = M4_cap_screw;            // Used with nuts when sheets are thin
frame_thick_screw = M4_pan_screw;           // Used with tapped holes when sheets are thick and hard, e.g. plastic or metal
//
// Feature sizes
//
default_wall = 3;
thick_wall = 4;

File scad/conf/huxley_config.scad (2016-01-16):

//
// Mendel90
//
// GNU GPL v2
// nop.head@gmail.com
// hydraraptor.blogspot.com
//
// Configuration file
//
echo("Huxley:");

Z_bearings = LM6UU;
Y_bearings = LM6UU;
X_bearings = LM6UU;

X_motor = NEMA14;
Y_motor = NEMA14;
Z_motor = NEMA14;

hot_end = JHeadMk5x;
extruder = Direct14;

X_travel = 152;
Y_travel = 150;
Z_travel = 150;

vero_bed = true;
x_holes = round(150 / 2.54) + 6;
y_holes = round(Y_travel / 2.54) + 4;

bed_depth = 160;        // 59 + 4 holes
bed_width = 165;        // 59 + 6 holes
bed_pillars = M3x20_pillar;
bed_glass = glass2;
bed_thickness = pcb_thickness + sheet_thickness(bed_glass);    // PCB heater plus glass sheet
bed_holes = [(x_holes - 3) * 2.54, (y_holes - 3) * 2.54];

base = DiBond;                  // Sheet material used for the base. Needs to be thick enough to screw into.
base_corners = 25;
base_nuts = true;
squeeze = true;

frame = DiBond;
frame_corners = 25;
frame_nuts = true;

case_fan = fan80x25;
part_fan = fan40x11;

psu = External;
controller = Melzi;
//raspberry_pi = true;
//raspberry_pi_camera = true;
//light_strip =  RIGID5050_208;

spool = spool_200x55;
bottom_limit_switch = false;
top_limit_switch = true;
include_fan = true;

clip_handles = false;
single_piece_frame = true;
stays_from_window = false;
cnc_sheets = true;                 // If sheets are cut by CNC we can use slots, etc instead of just round holes
pulley_type = GT2x20_metal_pulley;

Y_carriage = DiBond;

X_belt = GT2x6;
Y_belt = GT2x6;
motor_shaft = 5;
Z_screw_dia = 5;            // Studding for Z axis

Y_carriage_depth = bed_holes[1] + 7;
Y_carriage_width = bed_holes[0] + 7;

Z_nut_radius = M5_nut_radius;
Z_nut_depth = M5_nut_depth;
Z_nut = M5_nut;

//
// Default screw use where size doesn't matter
//
cap_screw = M3_cap_screw;
hex_screw = M3_hex_screw;
//
// Screw for the frame and base
//
frame_soft_screw = No4_screw;               // Used when sheet material is soft, e.g. wood
frame_thin_screw = M3_cap_screw;            // Used with nuts when sheets are thin
frame_thick_screw = M3_pan_screw;           // Used with tapped holes when sheets are thick and hard, e.g. plastic or metal
//
// Feature sizes
//
default_wall = 2;
thick_wall = 3;

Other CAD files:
Prusa_retrofit/prusa-z-motor-bracket.stl
scad/conf/dibond_E3D_config.scad
dibond/sheets/frame_base.dxf
dibond/sheets/frame_gantry.dxf
dibond/sheets/frame_gantry_and_y_carriage.dxf
dibond/sheets/frame_left.dxf
dibond/sheets/frame_right.dxf
dibond/sheets/frame_stays.dxf
dibond/sheets/y_heatshield.dxf
dibond/stls/accessories/light_and_camera_brackets.stl
dibond/stls/accessories/light_strip_bracket_left.stl
dibond/stls/accessories/light_strip_bracket_right.stl
dibond/stls/accessories/rpi_bracket.stl
dibond/stls/accessories/z_limit_switch_bracket.stl
dibond/stls/atx_long_bracket.stl
dibond/stls/atx_short_bracket.stl
dibond/stls/d_motor_bracket.stl
dibond/stls/d_motor_bracket_lid.stl
dibond/stls/d_shell.stl
dibond/stls/d_shell_lid.stl
dibond/stls/dust_filter.stl
dibond/stls/fixing_block.stl
dibond/stls/printed/atx_brackets.stl
dibond/stls/printed/bar_clamps.stl
dibond/stls/printed/cal.stl
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

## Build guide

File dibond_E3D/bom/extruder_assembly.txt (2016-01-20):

extruder_assembly:
Vitamins:
  3 Ball bearing 608 8mm x 22mm x 7mm
  3 M3 cap screw x 12mm
  3 M3 hex screw x 10mm
  1 M4 hex screw x 20mm
  2 M4 hex screw x 50mm
  1 M8 hex screw x 60mm, hobbed at 25
  3 Nut M3
  3 Nut M4
  2 Nut M8
  1 Smooth rod 8mm x 22mm
  2 Spring 7mm OD, 1mm gauge x 10mm long
  3 Washer M3 x 7mm x 0.5mm
  8 Washer M4 x 9mm x 0.8mm
  6 Star washer M3 x 0.5mm
  1 Star washer M8 x 1.6mm

Printed:
  1 wades_big_gear.stl
  1 wades_block.stl
  1 wades_gear_spacer.stl
  1 wades_idler_block.stl

Sub-assemblies:
  1 extruder_motor_assembly
  1 hot_end_assembly

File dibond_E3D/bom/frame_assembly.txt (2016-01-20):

frame_assembly:
Vitamins:
 36 M4 cap screw x 16mm
  2 Dibond sheet 166mm x 388mm x 3mm
  1 Dibond sheet 465mm x 388mm x 3mm
  1 Dibond sheet 465mm x 419mm x 3mm
 36 Nyloc nut M4
  2 AL square tube 12.7 x 12.7 x 1.63 x 400mm
 40 Washer M4 x 9mm x 0.8mm
 10 Ziptie 100mm min length

Printed:
  8 fixing_block.stl
  2 rear_fixing_block.stl
  1 ribbon_clamp_20_44N.stl
  1 ribbon_clamp_26_44N.stl
  4 tube_cap.stl

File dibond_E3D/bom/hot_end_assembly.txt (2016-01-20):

hot_end_assembly:
Vitamins:
  1 Fan 30mm x 10mm
  1 E3D V6 direct 3mm
  1 Heatshrink sleeving ID 6.4mm x 60mm
  1 Ziptie 100mm min length

Printed:

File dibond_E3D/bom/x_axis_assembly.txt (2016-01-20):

x_axis_assembly:
Vitamins:
  1 Belt T2 x 6mm x 860mm
  1 M4 hex screw x 20mm
  2 Smooth rod 8mm x 381mm
  1 Wingnut M4

Printed:

Sub-assemblies:
  1 extruder_assembly
  1 x_carriage_assembly
  1 x_carriage_fan_assembly

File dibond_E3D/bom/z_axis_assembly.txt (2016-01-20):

z_axis_assembly:
Vitamins:
  2 M3 cap screw x 16mm
  4 M4 cap screw x 16mm
  2 Brass nut M6
  2 Nyloc nut M3
  4 Nyloc nut M4
  2 No2 pan wood screw x 13mm
  2 Smooth rod 8mm x 340mm
  1 Microswitch
  2 Threaded rod M6 x 300mm
  2 Washer M2.5 x 5.9mm x 0.5mm
  2 Washer M3 x 7mm x 0.5mm
  4 Washer M4 x 9mm x 0.8mm

Printed:
  2 z_bar_clamp.stl
  2 z_screw_pointer.stl

Sub-assemblies:
  1 x_idler_assembly
  1 x_motor_assembly
  2 z_motor_assemblies

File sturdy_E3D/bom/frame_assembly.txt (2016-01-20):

frame_assembly:
Vitamins:
  2 MDF sheet 162mm x 389mm x 12mm
  1 MDF sheet 489mm x 389mm x 12mm
  1 MDF sheet 489mm x 436mm x 12mm
 39 No6 pan wood screw x 16mm
 39 Washer M4 x 9mm x 0.8mm
 39 Star washer M4 x 0.8mm

Printed:
  2 cable_clip_AB.stl
  2 cable_clip_AD.stl
  1 cable_clip_CA.stl
 10 fixing_block.stl
  1 ribbon_clamp_20_40.stl
  1 ribbon_clamp_26_40.stl

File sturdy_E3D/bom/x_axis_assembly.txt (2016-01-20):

x_axis_assembly:
Vitamins:
  1 Belt T2 x 6mm x 904mm
  1 M4 hex screw x 20mm
  2 Smooth rod 10mm x 403mm
  1 Wingnut M4

Printed:

Sub-assemblies:
  1 extruder_assembly
  1 x_carriage_assembly
  1 x_carriage_fan_assembly

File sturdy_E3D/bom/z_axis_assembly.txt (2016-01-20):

z_axis_assembly:
Vitamins:
  2 M4 cap screw x 20mm
  2 Brass nut M8
  2 Nyloc nut M4
  2 No2 pan wood screw x 13mm
  4 No6 pan wood screw x 16mm
  2 Smooth rod 10mm x 340mm
  1 Microswitch
  2 Threaded rod M8 x 300mm
  2 Washer M2.5 x 5.9mm x 0.5mm
  6 Washer M4 x 9mm x 0.8mm
  4 Star washer M4 x 0.8mm

Printed:
  2 z_bar_clamp.stl
  2 z_screw_pointer.stl

Sub-assemblies:
  1 x_idler_assembly
  1 x_motor_assembly
  2 z_motor_assemblies

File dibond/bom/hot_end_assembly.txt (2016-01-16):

hot_end_assembly:
Vitamins:
  1 JHead MK5 hot end 3mm
  1 110mm x 25mm self amalgamating silicone tape
  2 PTFE sleeving OD 1.2mm ID 0.71mm x 62mm
  2 Heatshrink sleeving ID 1.6mm x 15mm
  2 PTFE sleeving OD 2.6mm ID 2mm x 45mm
  1 Heatshrink sleeving ID 6.4mm x 60mm
  2 Red PTFE wire 16/0.2 length 170mm
  1 Ziptie 100mm min length

Printed:

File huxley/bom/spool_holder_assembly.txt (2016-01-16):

spool_holder_assembly:
Vitamins:
  4 Ball bearing 608 8mm x 22mm x 7mm
  2 M3 cap screw x 16mm
  4 M8 cap screw x 30mm
  1 Foam sponge 20mm x 20mm x 20mm
  2 Nyloc nut M3
  4 Nyloc nut M8
  1 PLA sample 1.75mm ~50m
  1 PTFE tubing OD 4.6mm ID 3.84mm x 750mm
  2 Washer M3 x 7mm x 0.5mm
 12 Washer M8 x 17mm x 1.6mm
  4 Washer M8 x 30mm x 1.5mm

Printed:
  1 dust_filter.stl
  2 spool_bracket_female.stl
  2 spool_bracket_male.stl

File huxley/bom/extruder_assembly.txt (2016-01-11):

extruder_assembly:
Vitamins:
  1 Ball bearing 624 4mm x 13mm x 5mm
  4 M3 cap screw x 16mm
  1 M3 cap screw x 25mm
  1 M4 cap screw x 35mm
  1 M4 hex screw x 16mm
  2 M4 hex screw x 20mm
  5 Nut M3
  1 Nut M4
  1 Nyloc nut M4
  3 M3 pan screw x 8mm
  1 Spring 6.5mm OD, 0.96mm gauge x 16mm long
 10 Washer M3 x 7mm x 0.5mm
  7 Washer M4 x 9mm x 0.8mm
  8 Star washer M3 x 0.5mm

Printed:
  1 direct_block.stl
  1 direct_idler_lever.stl

Sub-assemblies:
  1 extruder_motor_assembly
  1 hot_end_assembly

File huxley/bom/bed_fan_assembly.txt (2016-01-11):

bed_fan_assembly:
Vitamins:
  4 M4 cap screw x 16mm
  1 Fan 80mm x 25mm
  4 Nyloc nut M4
  4 Washer M4 x 9mm x 0.8mm

Printed:
  1 fan_guard.stl

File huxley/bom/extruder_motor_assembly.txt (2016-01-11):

extruder_motor_assembly:
Vitamins:
  2 M3 cap screw x 35mm
  1 M3 grub screw x 3mm
  1 hobbed pulley 8x5
  1 NEMA14 x 36mm stepper motor
  2 Nut M3
  2 No2 pan wood screw x 13mm
  2 Washer M2.5 x 5.9mm x 0.5mm
  2 Washer M3 x 7mm x 0.5mm

Printed:
  1 d_motor_bracket.stl
  1 d_motor_bracket_lid.stl

Sub-assemblies:
  1 extruder_connection_pcb_assembly

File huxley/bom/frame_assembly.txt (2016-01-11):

frame_assembly:
Vitamins:
  2 M3 cap screw x 10mm
 34 M3 cap screw x 16mm
  2 Dibond sheet 122mm x 317mm x 3mm
  1 Dibond sheet 356mm x 313mm x 3mm
  1 Dibond sheet 356mm x 317mm x 3mm
 36 Nyloc nut M3
  2 AL square tube 12.7 x 12.7 x 1.63 x 294mm
 36 Washer M3 x 7mm x 0.5mm
 10 Ziptie 100mm min length

Printed:
  8 fixing_block.stl
  2 rear_fixing_block.stl
  1 ribbon_clamp_20_33N.stl
  1 ribbon_clamp_26_33N.stl
  4 tube_cap.stl

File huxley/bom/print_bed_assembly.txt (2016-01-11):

print_bed_assembly:
Vitamins:
  4 19mm bulldog clip
  1 PCB bed 165mm x 160mm
  4 Corrugated cardboard 149mm x 159mm x 5mm
  4 M3 cap screw x 10mm
  1 Glass sheet 150mm x 160mm x 2mm
  4 Hex male / female pillar M3 x 20mm
  1 Polypropylene strip 224mm x 33mm x 0.5mm
  1 Ribbon cable 26 way 334mm
  2 Heatshrink sleeving ID 1.6mm x 15mm
  2 Heatshrink sleeving ID 2.4mm x 15mm
  2 Heatshrink sleeving ID 6.4mm x 30mm
  1 Epcos B57861S104F40 100K 1% thermistor
  4 Washer M3 x 7mm x 0.5mm
  1 Black wire 32/0.2 length 635mm
  1 Red wire 32/0.2 length 620mm

Printed:

Sub-assemblies:
  1 y_carriage_assembly

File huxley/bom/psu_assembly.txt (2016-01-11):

psu_assembly:
Vitamins:
  1 IEC mains lead
  1 PSU e.g. LAPTOPPSU

Printed:

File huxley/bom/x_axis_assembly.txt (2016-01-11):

x_axis_assembly:
Vitamins:
  1 Belt T2 x 6mm x 690mm
  2 Smooth rod 6mm x 287mm
  2 Wingnut M4

Printed:

Sub-assemblies:
  1 extruder_assembly
  1 x_carriage_assembly
  1 x_carriage_fan_assembly

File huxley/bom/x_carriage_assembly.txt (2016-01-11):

x_carriage_assembly:
Vitamins:
  2 M3 cap screw x 16mm
  1 M3 cap screw x 20mm
  2 M3 cap screw x 25mm
  3 LM6UU linear bearing
  1 Nut M3
  4 Nyloc nut M3
  4 Washer M3 x 7mm x 0.5mm
  3 Ziptie 100mm min length

Printed:
  1 x_belt_clamp.stl
  1 x_belt_grip.stl
  1 x_belt_tensioner.stl
  1 x_carriage.stl

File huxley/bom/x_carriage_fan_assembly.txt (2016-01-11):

x_carriage_fan_assembly:
Vitamins:
  4 M3 cap screw x 25mm
  1 Fan 40mm x 11mm
  4 Nyloc nut M3
  4 Washer M3 x 7mm x 0.5mm

Printed:
  1 x_carriage_fan_bracket.stl
  1 x_carriage_fan_duct.stl

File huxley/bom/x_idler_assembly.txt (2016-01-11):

x_idler_assembly:
Vitamins:
  2 Ball bearing 624 4mm x 13mm x 5mm
  8 M3 cap screw x 16mm
  1 M4 cap screw x 45mm
  2 LM6UU linear bearing
  8 Nyloc nut M3
  1 Nyloc nut M4
  8 Washer M3 x 7mm x 0.5mm
  2 Washer M4 x 9mm x 0.8mm
  2 Washer M5 x 20mm x 1.4mm

Printed:
  2 x_end_clamp.stl
  1 x_idler_bracket.stl

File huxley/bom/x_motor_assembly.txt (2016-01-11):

x_motor_assembly:
Vitamins:
 12 M3 cap screw x 16mm
  2 M3 cap screw x 20mm
  2 M3 cap screw x 35mm
  1 15 way D IDC socket
  2 M3 grub screw x 6mm
  2 M3 hex screw x 16mm
  2 LM6UU linear bearing
  1 NEMA14 x 36mm stepper motor
 14 Nyloc nut M3
  2 Nitrile O-ring 2.5mm x 1.6mm
  1 Polypropylene strip 315mm x 18mm x 0.5mm
  1 Polypropylene strip 389mm x 25mm x 0.5mm
  2 M3 pan screw x 8mm
  4 No2 pan wood screw x 13mm
  1 GT2 pulley 20 teeth
  1 Ribbon cable 20 way 1074mm
  1 Microswitch
  4 Heatshrink sleeving ID 2.4mm x 15mm
  4 Washer M2.5 x 5.9mm x 0.5mm
 23 Washer M3 x 7mm x 0.5mm
  2 Star washer M3 x 0.5mm

Printed:
  1 d_shell.stl
  1 d_shell_lid.stl
  1 ribbon_clamp_14_33.stl
  1 ribbon_clamp_14_33NB.stl
  1 ribbon_clamp_20_33H.stl
  2 x_end_clamp.stl
  1 x_motor_bracket.stl
  1 x_motor_ribbon_bracket.stl

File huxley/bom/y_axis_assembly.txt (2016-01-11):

y_axis_assembly:
Vitamins:
  1 Belt T2 x 6mm x 512mm
 12 M3 cap screw x 16mm
 12 Nyloc nut M3
  2 No2 pan wood screw x 13mm
  1 Smooth rod 6mm x 209mm
  1 Smooth rod 6mm x 311mm
  1 Microswitch
  2 Washer M2.5 x 5.9mm x 0.5mm
 12 Washer M3 x 7mm x 0.5mm

Printed:
  3 y_bar_clamp.stl
  1 y_bar_clamp_switch.stl

Sub-assemblies:
  1 print_bed_assembly
  1 y_idler_assembly
  1 y_motor_assembly

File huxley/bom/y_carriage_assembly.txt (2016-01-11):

y_carriage_assembly:
Vitamins:
 14 M3 cap screw x 16mm
  2 M3 cap screw x 20mm
  1 Dibond sheet 164mm x 159mm x 3mm
  3 LM6UU linear bearing
 16 Nyloc nut M3
 16 Washer M3 x 7mm x 0.5mm
  3 Ziptie 100mm min length

Printed:
  1 ribbon_clamp_26_33.stl
  1 ribbon_clamp_26_33N.stl
  3 y_bearing_mount.stl
  1 y_belt_anchor.stl
  1 y_belt_anchor_toothed.stl
  1 y_belt_clip.stl
  1 y_belt_clip_toothed.stl

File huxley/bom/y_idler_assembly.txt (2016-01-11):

y_idler_assembly:
Vitamins:
  2 Ball bearing 624 4mm x 13mm x 5mm
  1 M3 cap screw x 16mm
  1 M4 cap screw x 30mm
  1 Nyloc nut M3
  1 Nyloc nut M4
  1 Washer M3 x 7mm x 0.5mm
  4 Washer M4 x 9mm x 0.8mm
  2 Washer M5 x 20mm x 1.4mm

Printed:
  1 y_idler_bracket.stl

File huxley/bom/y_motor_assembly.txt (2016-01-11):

y_motor_assembly:
Vitamins:
  4 M3 cap screw x 16mm
  2 M3 grub screw x 6mm
  1 NEMA14 x 36mm stepper motor
  4 Nyloc nut M3
  4 M3 pan screw x 8mm
  1 GT2 pulley 20 teeth
  8 Washer M3 x 7mm x 0.5mm
  4 Star washer M3 x 0.5mm

Printed:
  1 y_motor_bracket.stl

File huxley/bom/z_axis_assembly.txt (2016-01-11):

z_axis_assembly:
Vitamins:
  6 M3 cap screw x 16mm
  2 Brass nut M5
  6 Nyloc nut M3
  2 No2 pan wood screw x 13mm
  2 Smooth rod 6mm x 280mm
  1 Microswitch
  2 Threaded rod M5 x 244mm
  2 Washer M2.5 x 5.9mm x 0.5mm
  6 Washer M3 x 7mm x 0.5mm

Printed:
  2 z_bar_clamp.stl
  2 z_screw_pointer.stl

Sub-assemblies:
  1 x_idler_assembly
  1 x_motor_assembly
  2 z_motor_assemblies

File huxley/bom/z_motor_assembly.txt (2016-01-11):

z_motor_assemblies:
Vitamins:
 14 M3 cap screw x 16mm
  2 NEMA14 x 36mm stepper motor
 14 Nyloc nut M3
  8 M3 pan screw x 8mm
  2 Neoprene tubing OD 8mm ID 5mm x 15mm
 22 Washer M3 x 7mm x 0.5mm
  8 Star washer M3 x 0.5mm

Printed:
  4 z_coupling.stl
  1 z_motor_bracket_lhs.stl
  1 z_motor_bracket_rhs.stl

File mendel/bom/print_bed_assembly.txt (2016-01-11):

print_bed_assembly:
Vitamins:
  4 19mm bulldog clip
  1 PCB bed 214mm x 214mm
  4 Corrugated cardboard 201mm x 217mm x 5mm
  4 M3 cap screw x 10mm
  1 Glass sheet 214mm x 202mm x 2mm
  4 Hex male / female pillar M3 x 20mm
  1 Polypropylene strip 271mm x 33mm x 0.5mm
  1 Ribbon cable 26 way 381mm
  2 Heatshrink sleeving ID 1.6mm x 15mm
  2 Heatshrink sleeving ID 2.4mm x 15mm
  2 Heatshrink sleeving ID 6.4mm x 30mm
  1 Epcos B57861S104F40 100K 1% thermistor
  4 Washer M3 x 7mm x 0.5mm
  1 Black wire 32/0.2 length 635mm
  1 Red wire 32/0.2 length 620mm

Printed:

Sub-assemblies:
  1 y_carriage_assembly

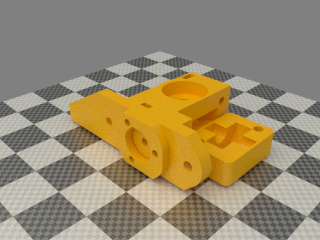
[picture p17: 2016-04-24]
dibond/render/printed/wades_extruder.png

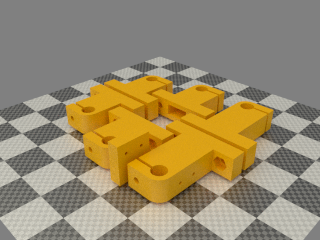
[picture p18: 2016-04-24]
dibond/render/printed/bar_clamps.png

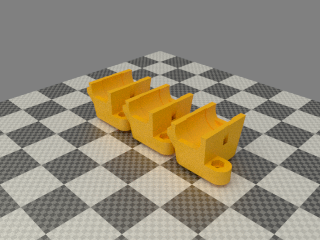
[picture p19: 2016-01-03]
dibond/render/printed/y_bearing_mounts.png

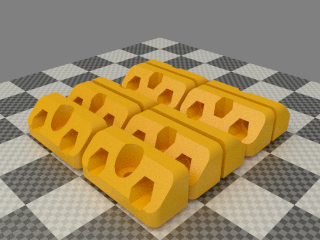
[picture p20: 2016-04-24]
dibond/render/printed/fixing_blocks.png

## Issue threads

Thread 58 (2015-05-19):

Frame martial thickness affect wrong dillhole positions

BadKarmaPete, 2015-05-19:
There is a small Issue when creating your own Mende90 with different frame material. The Postion of a few drillholes is affected by the thickness of the choosen material. So when I create my own Mendel90 with MDF12 plates the drillholes for the fixing blocks moving a little bit up or exactly, away from the edge (around 1mm). This makes it difficult to build the frame.

nophead, 2015-05-19:
Not sure what you mean. The sturdy version uses 12mm MDF and all the screw holes come out in the right place.

BadKarmaPete, 2015-05-19:
Ok I've done a mistake. The frame thickness doesn't affect the hole postion. It only seems that the hole is moving, i've meassured the distance between the center of the hole and the edge. The distance is changing when using different screws with different diameters.
For explanation, I was assuming that the drill holes are aligned with their center, but after printing the drillguide from the sturdy version and holding it together with my printed fixing block I see that their are aligned on the outer diameter.

Thank you for your fast response and sorry for my Issue report.

Greetings from Germany

nophead, 2015-05-19:
Still not sure what you mean exactly. If you make the sheets thicker the gantry fixing blocks will move backwards so the holes will be further back. If you make the screws bigger the fixing blocks will get bigger so I think the hole centres probably move back a little as well.

In all situations the drill templates should mark the centre of the hole. In the case of the versions not made by CNC the fixing blocks have slots but the drill centre should still be in the middle of the slot. The slots allow 1mm adjustment either way in case the drilling is not accurate. I used an optical centre punch and a spot drill to get very accurate holes before I started using CNC.

BadKarmaPete, 2015-05-20:
It's my fault, I thought the whole time that the fixing blocks doesn't change their size and only the holes change the diameter by the choosen screw. And after designing the second Mendel90 with MDF plates I failed to see any difference between the fixing blocks of the Dibond and MDF version, so i don't printed the newer ones and thought that the Dibond version should also fit.

nophead, 2015-05-21:
The Dibond fixing blocks have nut traps for M4 nuts but the ones for MDF have slots for wood screws and washers, so they are quite different.

Closed 2016-01-05.

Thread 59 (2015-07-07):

Mendel90 Kits

Masterrenny, 2015-07-07:
Hello,

Not sure how else I can contact you, but do you still offer/sell the kits and if so how much would one cost (UK) or would it be cheaper for me to get the parts myself?

Do you have a template for the frames and everything else? Or a manual I can follow for it as I can't seem to find one. Or a parts list.

Regards
Thomas

nophead, 2015-07-07:
Yes we sell full kits for the CNC cut dibond version and some parts for the other versions, see http://forums.reprap.org/read.php?94,196585.

If you want to completely self source and don't have access to a CNC router the MDF sturdy version can be made with drill templates found here: https://github.com/nophead/Mendel90/tree/master/sturdy/sheets and the parts list here: https://github.com/nophead/Mendel90/blob/master/sturdy/bom/bom.txt.

Self sourcing will cost less, but not a lot less, because of one off prices and lots of postage from different sources and it will be a lot more work.

nophead, 2016-01-06:
We no longer sell kits.

guerd87, 2016-03-31:
Do you still sell printed parts? Im looking for a complete set of parts including extruder for MDF version

nophead, 2016-04-01:
Yes we still sell the parts listed here: http://forums.reprap.org/read.php?94,567445

Closed 2016-01-06.

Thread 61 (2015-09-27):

Dibond crashes at Z_max + X_min

PaulCornelissen, 2015-09-27:
The Dibond version crashes the extruder motor into the into the top z-bar clamp.

This has happened to me a couple of times now. When homing the z-axis while at X-min the extruder motor hits the top z-bar clamp. This prevents the limit-switch from being hit so the motors won't stop running. This causes the z-bar clamp to move out of place and messes up the calibration of the z-length. Steps will also be missed and this causes you to lose the levelling calibration. Also if you're not quick to turn the power of the other z-bar clamp will also be hit. I've replaced them both by now.

Here's a photo of this in practice:
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

I don't know if this is a known issue all ready, but I've opened up an issue here because today I found out this bug is also in the models:
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

Set these three lines almost at the top of ```main.scad```:

    X = 1 * X_travel / 2; // - limit_switch_offset;
    Y = 0 * Y_travel / 2; // - limit_switch_offset;
    Z = 1 * Z_travel;

nophead, 2015-09-27:
It is a known issue (with no simple fix) but at X_MAX, not X_MIN. You should always home X before Z and then it never happens.

nophead, 2015-09-27:
Actually the start.gcode script provided homes Z first but the end.gcode leaves the extruder at the right, so the next start never crashes. The only way it could crash is with manual actions or if it happened to be printing on the left extreme and was interrupted. Basically it never happens in normal use, which is why I didn't fix it. Hundreds of kits were built before anybody noticed.

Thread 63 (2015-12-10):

sturdy version with dados instead of fixing blocks, offset for gantry and L/R stays?

dangasaur, 2015-12-10:
I'm going to make a version of the sturdy with 3/4" MDF and instead of using the fixing blocks I want to just put a dado in the base for the gantry and stays.  I also want to put dados on either side of the gantry and base for the stays but that dimension seems less critical.

My plan was to simply increase the height of the gantry by the depth of my dado and reference the drill template from the top.

I'm trying to decipher the scad files to see where I can echo/print out the offset of the gantry from the front or rear of the base as well as the left and right stays.  Can you provide any guidance to get these dimensions?

I was also planning on just reducing the screw count etc in my head but a way to simply exclude all the fixing blocks would also be helpful.

nophead, 2015-12-10:
Hi,
   Had to Google "dado" as it doesn't have the same meaning in the UK.

   gantry_Y is the Y ordinate of the front edge of the gantry. You would need to add base_depth / 2 to get the distance from the front of the base sheet.

left_stay_x and right_stay_x are the X ordinates of the centrelines of the stays.

The fixing_blocks module defined in scad/main.scad places the fixing blocks and their holes and fasteners, etc. If you make it an empty module I think it will fix the bom and drill templates.

dangasaur, 2015-12-12:
Awesome, I think I've correctly located the gantry and the stays now.
Removing the fixing blocks worked as you said.

Thanks for your help.

Closed 2016-01-01.

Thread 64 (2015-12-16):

E3D with GT2 pulleys

dangasaur, 2015-12-16:
I see that the E3D branch does not have the GT2 pulley changeset.  Looking through the change set it seems like this is just a materials change and does not affect any printed parts (minus the removed T5 printed pulleys).  Is that correct?

nophead, 2015-12-16:
No the printed parts will change as the belt is a different thickness and the belt clips have teeth in them.

nophead, 2016-01-20:
master branch now supports E3D and uses GT2 pulleys.

Closed 2016-01-20.

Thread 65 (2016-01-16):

e3D wades block, recessed flat spot

dangasaur, 2016-01-16:
After printing the wades block for the e3d hot end I'm seeing that the hole where the hot end is inserted into the block has a flat spot or is "keyed" yet the hot end itself has no flat spot and is perfectly round.

I feel like I'm missing something but I cannot see how this is supposed to fit together.  What am I doing wrong?

nophead, 2016-01-16:
It is a truncated tear drop shape to allow it to be printed without support, as are all the horizontal holes. The flat is tangential to the circle, so shouldn't prevent a cylindrical hot end going in.

dangasaur, 2016-01-16:
Ah ok, that makes sense.  This must have just been a bad print.

nophead, 2016-01-16:
Yes if your bridges droop you might need to pare some away with knife.

dangasaur, 2016-01-17:
Just in case anyone comes across this at a later date, I concluded that this particular part had a poor print quality from my supplier.  I also discovered a few additional modifications needed for my e3D 1.75 universal hot end.

1. touch up the mounting hole with a 5/8ths forstner bit
2. drill out the filament hole with a #21 drill bit (.159") to fit the ptfe tubing
3. countersink a 9/32nds hole in the mounting hole to provide space for the ptfe coupler

At some point I will learn SCAD and incorporate these modifications for the 2nd printer I am building.

nophead, 2016-01-17:
You don't really want the gearing that Wades provides for 1.75mm filament. A direct drive extruder is better.

lexmark-benmarks, 2016-01-18:
Based on your comment I ended up having a set of 1:1 extruder gears printed.  My plan is to keep moving forward with what I have at this point and then change to a compatible direct drive extruder as soon as possible.

Thanks again for your feedback.

Closed 2016-01-16.

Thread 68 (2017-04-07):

Compile crashes at 'frame_base.dxf'

helifino, 2017-04-07:
Copied a conf file, didn't make any changes. Compile fails.
Linux Mint 17
Python 2.7.6
OpenSCAD version 2014.01.29

[mysturdy_E3D_config.scad.txt](https://github.com/nophead/Mendel90/files/904577/mysturdy_E3D_config.scad.txt)

[openscad.log.txt](https://github.com/nophead/Mendel90/files/904573/openscad.log.txt)

nophead, 2017-04-07:
README.md states OpenSCAD-2015.05 or later is required, so that is probably the reason it doesn't work.

helifino, 2017-04-07:
Indeed, this is the bit I was missing.

Closed 2017-04-07.

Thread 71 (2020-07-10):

Project description

hoijui, 2020-07-10:
Hey! :-)
could you maybe add a github repo description (plus tags), and also describe in the README on top what this project is (about)?
would be appreciated!
robin

nophead, 2020-07-10:
Not sure what you mean. Isn't the project description "A RepRap Mendel variant using sheets for the frame instead of rods"?

hoijui, 2020-07-10:
ouhhh... sorry! :D
indeed... I am not used to the new github look yet, sorry!

though it would be nice to have it in the README too.
should I make a PR for that?

nophead, 2020-07-10:
I have added it to the readme. Why the interest? This is an old project and I don't actively maintain it now.

hoijui, 2020-07-10:
I found to it from the open-manufacturing google group, where it was linked as someones motivation for building a library of standard parts for OpenSCAD and FreeCAD, because it is so well made. :-)

I am from OSE Germany, and we are working on.... stuff to improve the state of open hardware.

nophead, 2020-07-10:
If you want a library parts, see my other repository. https://github.com/nophead/NopSCADlib.

I developed it from the vitamins in Mendel90 but greatly improved them and I actively maintain it. If forms the basis of everything I 3D print and I am using it for my next 3D printer design.

hoijui, 2020-07-11:
oh WOW! :O
thank you!

I myself am a programmer, and thus OpenSCAD is more natural to me. Most of our tinkerers are mechanical engineers though, and they are all FreeCAD oriented. Do you have some way, or an idea, how to use your library there too?

nophead, 2020-07-11:
I think FreeCAD can import a OpenSCAD csg file, which is like the original source code except all the expressions have been replaced by constants and all the modules have been expanded to csg ops on primitives. I don't know if it supports all of OpenSCAD and I think you lose all the parametric aspects.

I think working with conventional CAD like FreeCAD you would import STEP files of components that a lot of manufacturers and other websites publish. They are more detailed and more accurate. I prefer to use OpenSCAD because I am a retired programmer, not a mechanical engineer. I also like the fact the representation of objects is human readable text, so it can be source controlled, etc, and I like the fact everything is 100% parametric by default.

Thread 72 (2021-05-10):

Stl

Gennadwed, 2021-05-10:
Здравствуйте, пытался загрузить stl файлы пишет нужен puch доступ.?

nophead, 2021-05-10:
All the STLs are already upload, so I don't know what you mean.

You can't upload anything to somebody else's project, to make additions you submit a push request that the owner can accept or reject.

Gennadwed, 2021-05-10:
Здравствуйте, да я их почему-то скачать не могу.

nophead, 2021-05-10:
Click on the file you want, e.g. https://github.com/nophead/Mendel90/blob/master/dibond/stls/atx_long_bracket.stl and then right click on the "Raw" button and select "save link as" in your browser context menu. Works for me in Chrome.

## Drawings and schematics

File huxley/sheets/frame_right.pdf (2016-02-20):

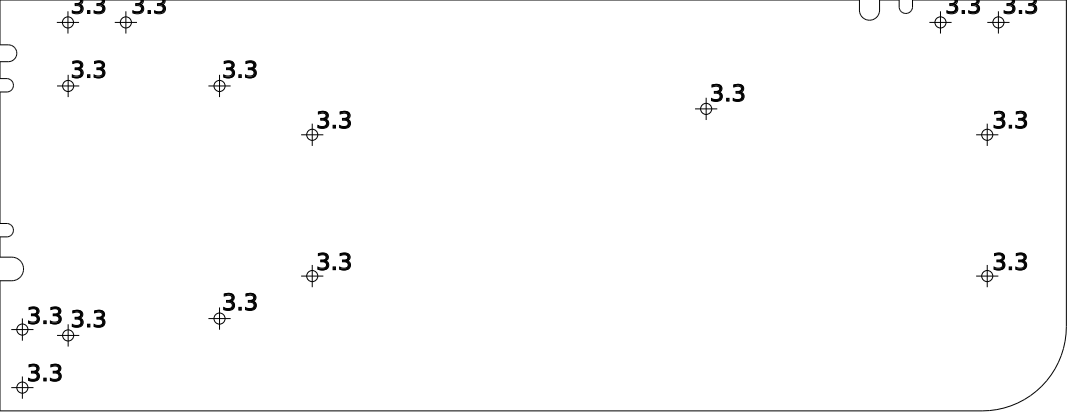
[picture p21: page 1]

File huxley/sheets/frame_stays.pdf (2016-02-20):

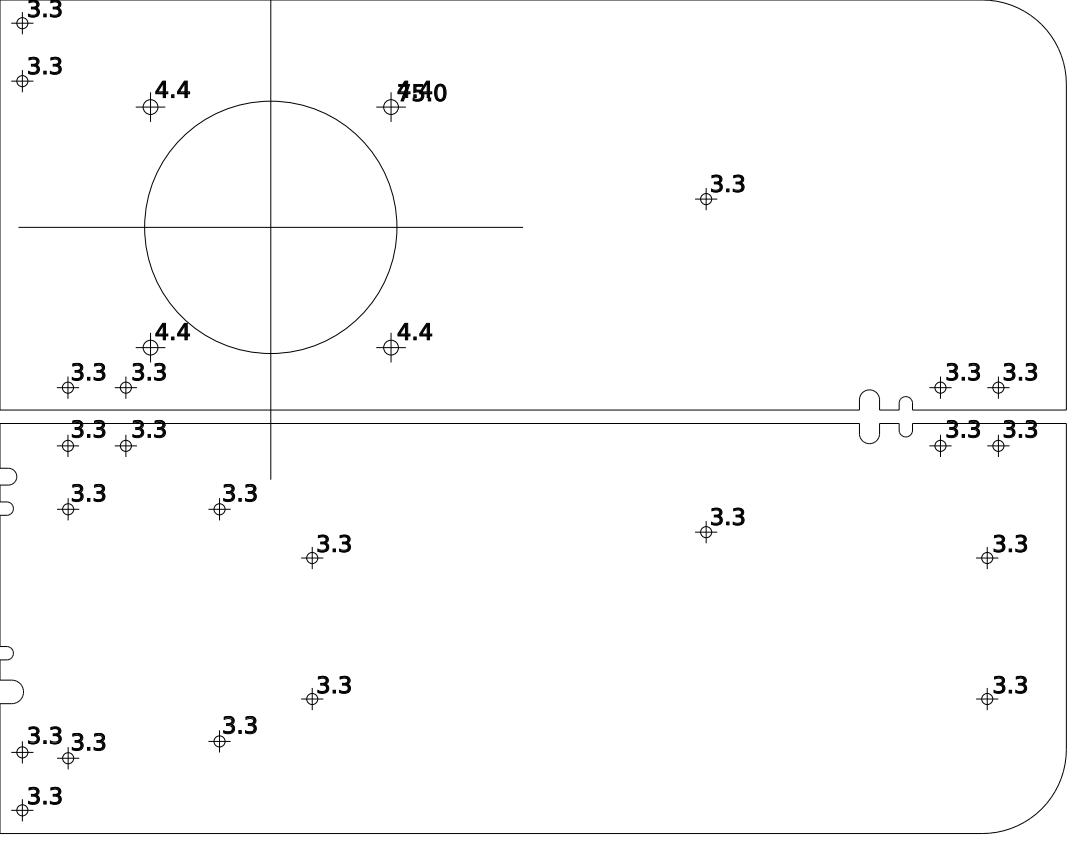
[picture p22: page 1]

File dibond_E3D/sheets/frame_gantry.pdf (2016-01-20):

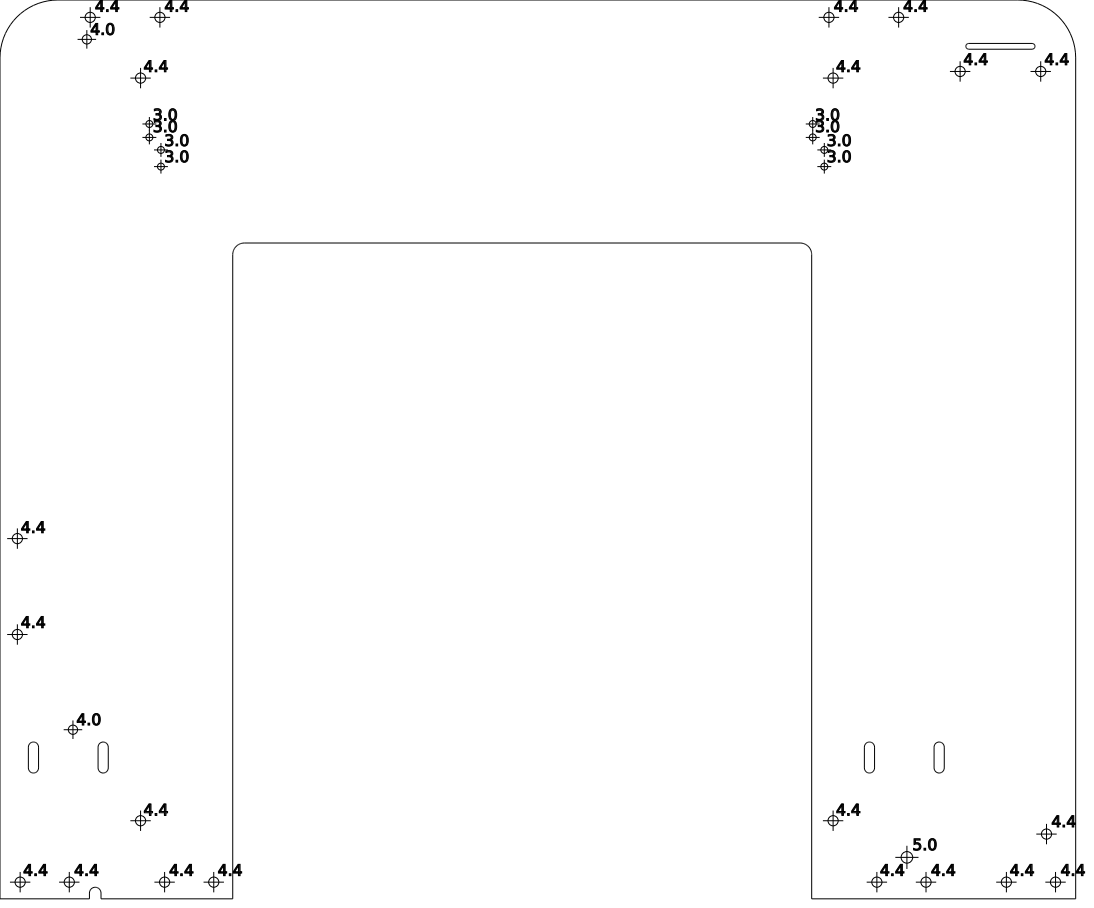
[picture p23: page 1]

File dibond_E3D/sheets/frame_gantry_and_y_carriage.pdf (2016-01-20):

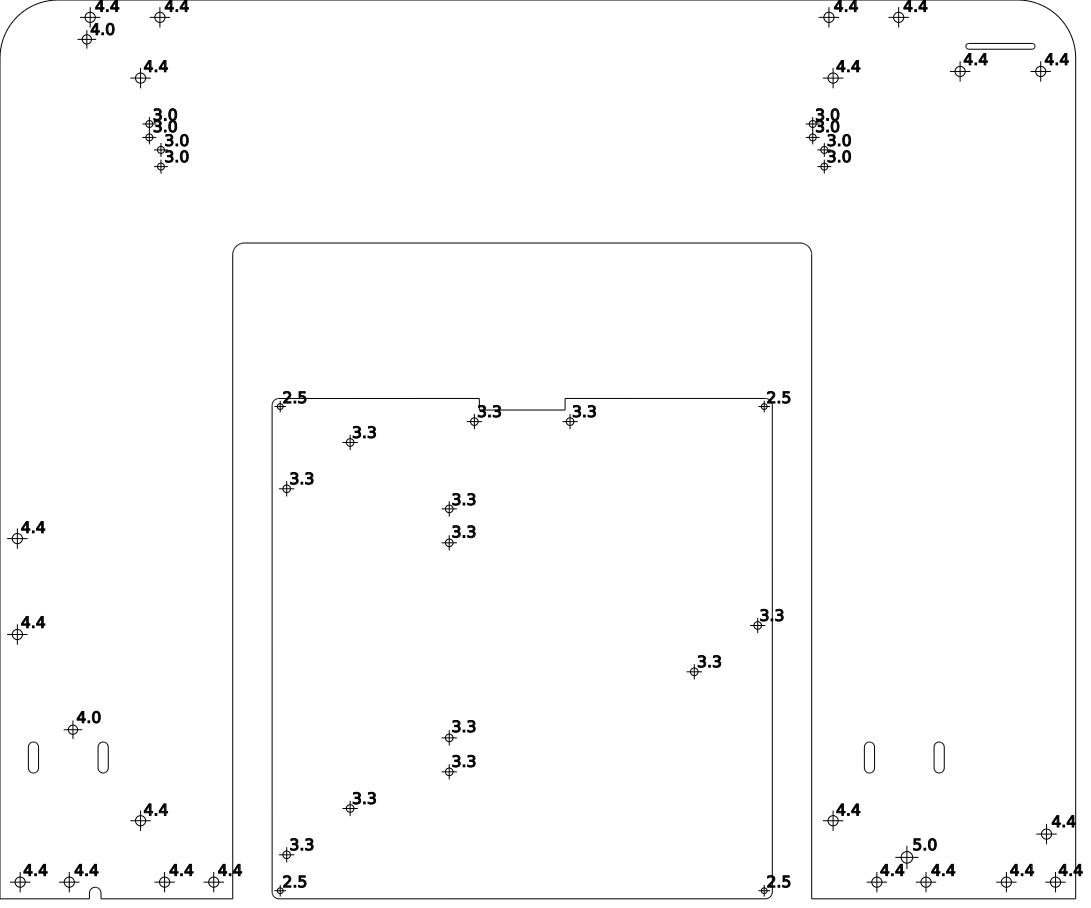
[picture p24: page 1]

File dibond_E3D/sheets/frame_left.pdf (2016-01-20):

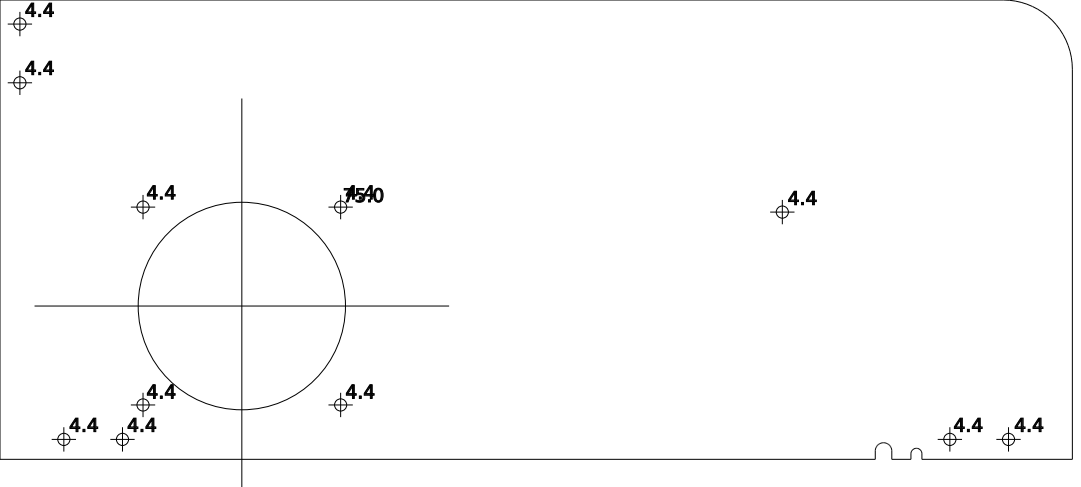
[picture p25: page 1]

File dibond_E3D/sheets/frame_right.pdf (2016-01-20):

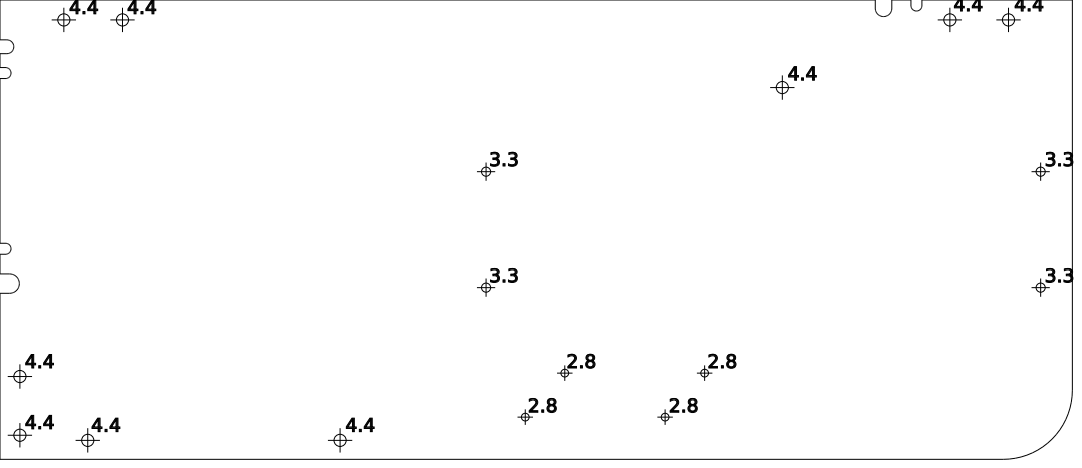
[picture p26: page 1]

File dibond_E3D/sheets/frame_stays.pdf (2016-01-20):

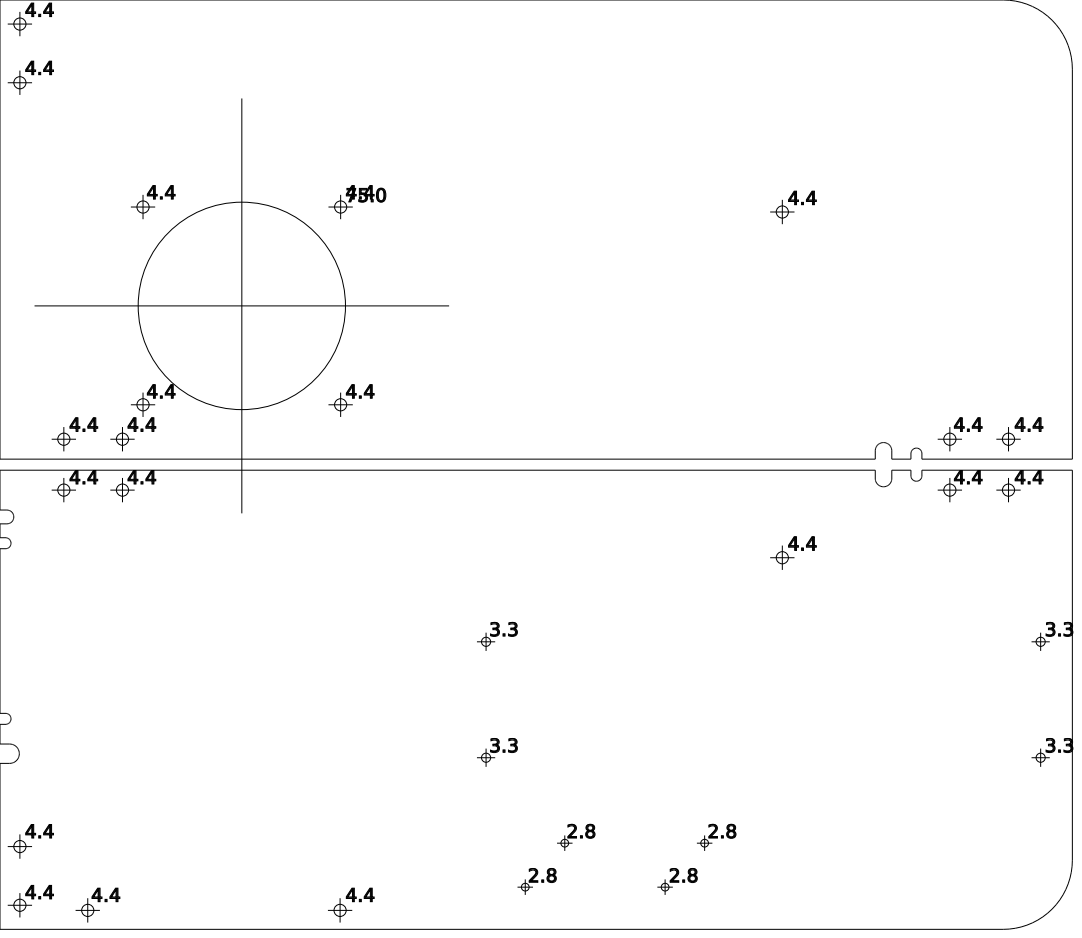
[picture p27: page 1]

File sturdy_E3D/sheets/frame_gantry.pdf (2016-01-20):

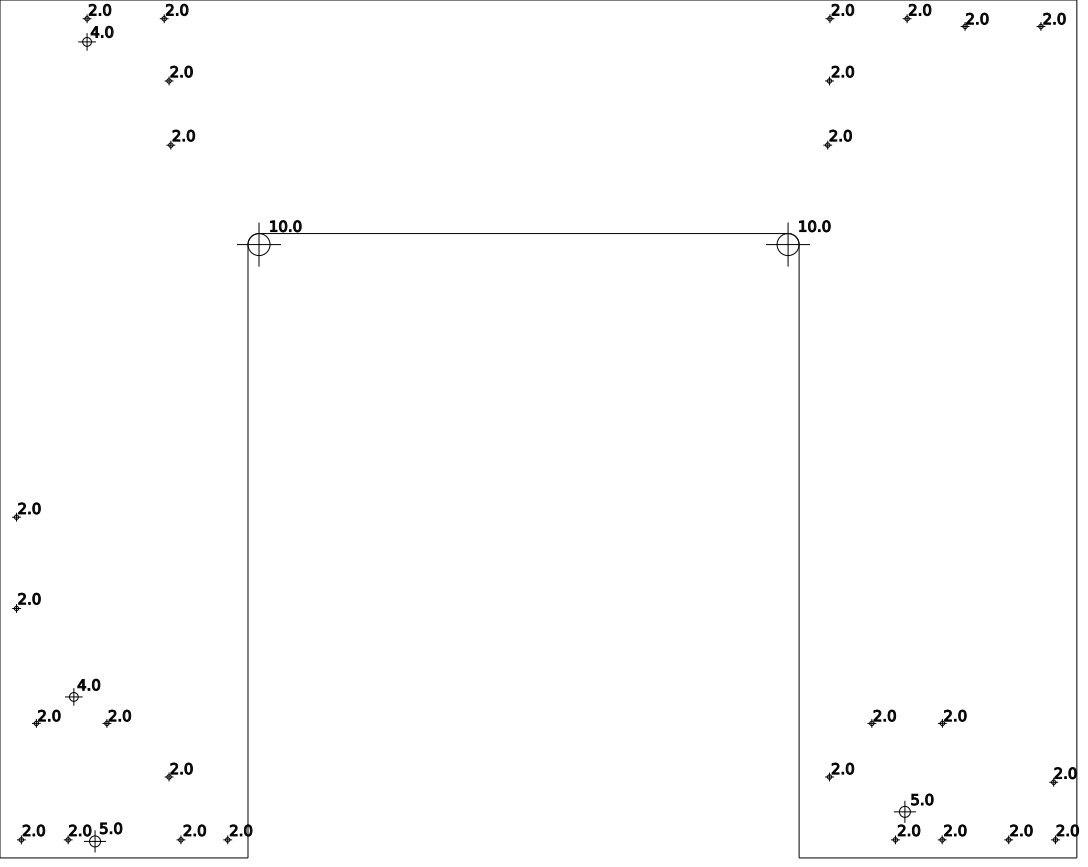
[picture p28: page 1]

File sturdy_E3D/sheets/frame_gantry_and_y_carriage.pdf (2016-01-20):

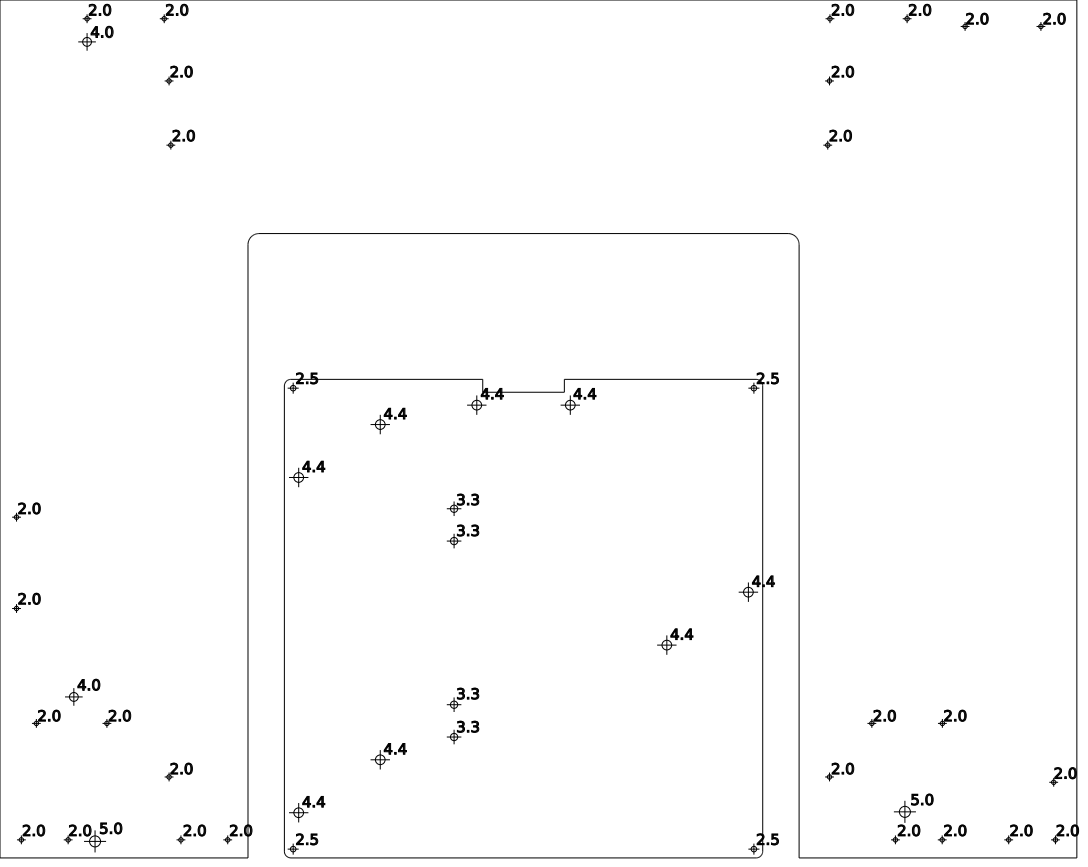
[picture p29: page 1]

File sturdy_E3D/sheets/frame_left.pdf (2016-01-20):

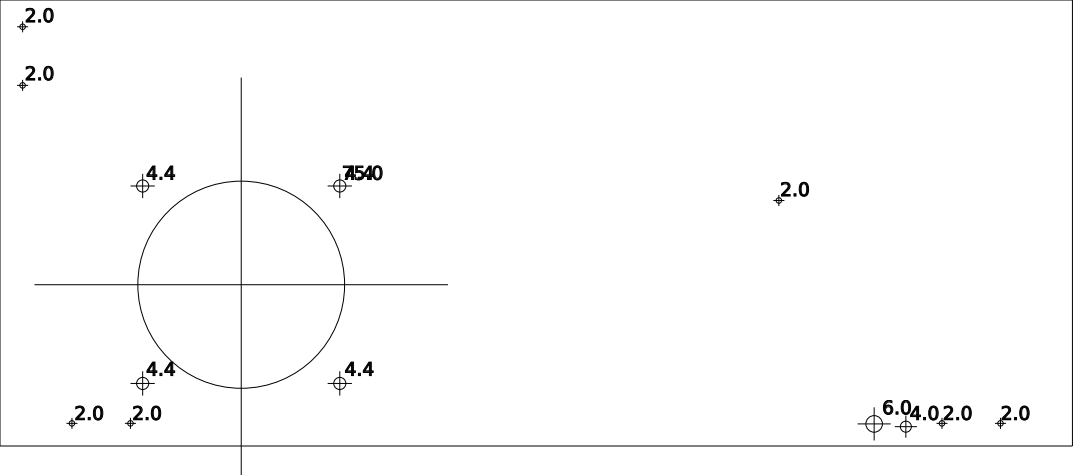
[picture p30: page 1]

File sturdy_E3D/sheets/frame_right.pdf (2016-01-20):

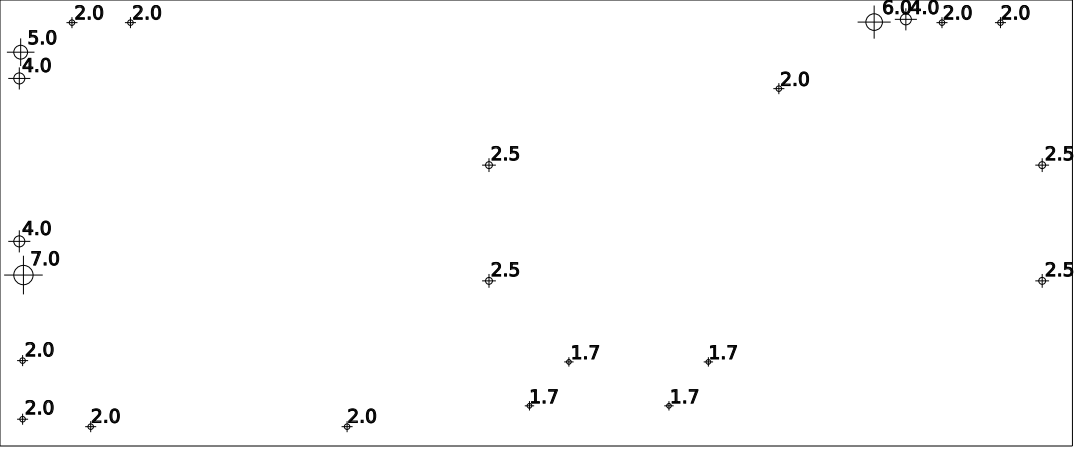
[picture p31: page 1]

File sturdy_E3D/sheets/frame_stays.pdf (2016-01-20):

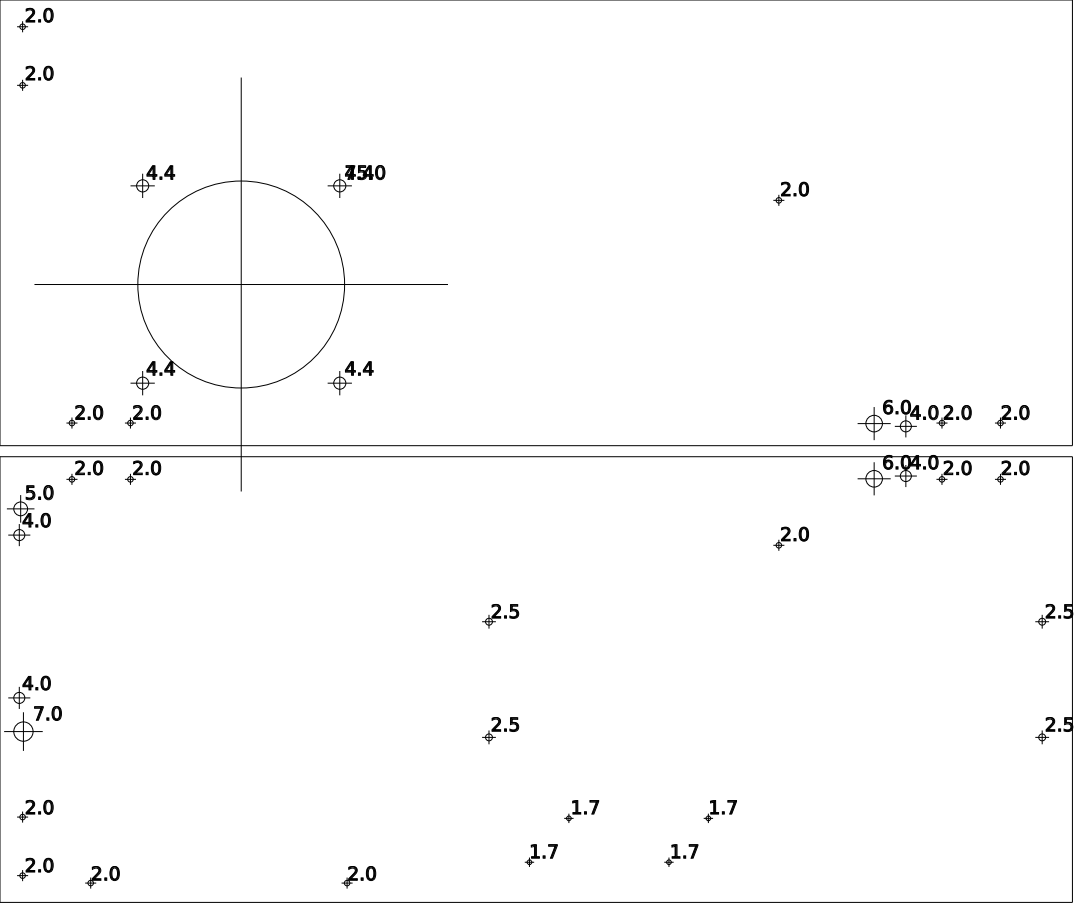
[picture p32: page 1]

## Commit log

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2012-03-13 Added a z-motor-bracket to allow the Mendel90 x-axis to be fitted to a Prusa. Merged credots into README.txt
    [prusa-z-motor-bracket.scad, prusa-z-motor-bracket.stl]
2012-03-13 Extracted all color resources into a common file.
    [ball-bearings.scad, bar-clamp.scad, bed.scad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]
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2012-03-13 Fixed replaced nut_grey with nut_color to match nuts.scad
    [colors.scad]
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2012-03-14 Changed wades hot end size to 16mm standard. It was set to 12, whoops.
    [wade.scad, wades_block.stl]
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2012-03-14 Glass thickness now defined by the glass object, like the other sheets.
    [bed.scad, config.scad, huxley_config.scad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]
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2012-03-16 Now combines some STLs into single files and puts all the ones that need printing the the plates directory. Added hash bangs for Linux users.
    [bar-clamp.scad, bar_clamps.stl, cable_clip.scad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]
2012-03-16 Renamed the plates directory "printed" and now copies the un-aggragated STLs rather than moving them. Added .gitignore
    [bar_clamps.stl, cable_clip_CA.stl, cable_clips.stl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]
2012-03-16 Sturdy STLs got missed from last commit
    [bar_clamps.stl, cable_clips.stl, cal.stl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]
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2012-03-16 Reworking color usage to support a "realistic" render mode, and a "design" render mode.
    [belts.scad, bulldog.scad, colors.scad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]
2012-03-16 Fixed last pull.
    [colors.scad, config.scad, huxley_config.scad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]
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2012-03-18 Added support for the Lulzbot/ebay PSU, including configurable screw types for mounting
    [electronics.scad, main.scad]
2012-03-21 Fixed crash when there is a part outside of any assembly
2012-03-22 Improved Wades extruder: Front moved back to allow for deeper hobbed bolts. Added upper support web and reduced the lower one to one layer. Added clamp option for experimental Mendel90 hot end. Added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
    [colors.scad, wade.scad, wades_block.stl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]
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2012-03-24 Turened up render too much , changed back to sane render time.
    rescaled back to 320x240 from 640x480 , turned intergrater down to 50 passes
    made grid objecy 200x200 mm.
    [render.blend]
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2012-04-01 Added the cardboard heat sheild. Tweaked the X belt length and the cable strip length. Now generates PDF versions of the sheets using Inkscape.
    [cable_strip.scad, frame_base_dxf.scad, frame_gantry_and_y_carriage_dxf.scad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]
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2012-04-02 Removed extra ribbon clamp that is included in d_motor_brackets.stl.
    [ribbon_clamp.scad, ribbon_clamps.stl]
2012-04-03 Heatshield spelling corrected and cable clearance sligtly bigger
    [main.scad, y_heatshield.dxf, y_heatshield_dxf.scad]
2012-04-03 Fixed spelling of y_heatshield()
    [main.scad]
2012-04-04 Added start washers to cable clips (screws too long otherwise). Cable strips 1mm narrower for more clearance in clips.
    [cable_clip.scad, cable_strip.scad, main.scad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]
2012-04-04 Added star washers to cable clips (screws too long otherwise). Cable strips 1mm narrower for more clearance in clips.
    [cable_clip.scad, cable_strip.scad, main.scad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]
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2012-11-15 This version used for the kits 1-6 at the GIST FOTM. Z axis length increased to 200mm. Added the Dibond variant that uses nuts in the parts instead of tapped holes. Added a ducted fan to the X carria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
    The extruder now has a groove mount for the JHead.
    Extruder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
    [ATX_PSU_brackets.scad, DiBond_config.scad, atx_brackets.stl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]
2012-11-17 This version used for kits 7- Nut traps moved further from the edge of most parts. Fixed ribbon clamp slots too deep. Modified for JHeadMK5. Changed bed thermsitor type. Extruder block is now thinner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
    Hobbed bolt not shows hob position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
    [ATX_PSU_brackets.scad, DiBond_config.scad, atx_brackets.stl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]
2012-11-26 Version used for kits 11+ Z cable made 100mm longer Manual updated
    [main.scad]
2012-12-07 Manual updated: fixed missing Z parts. Added skienforge and bed sections.
2012-12-09 Z bar clamps made both the same. Y bearing mounts made all the same and switch tab made smaller. Manual updated to reflect those changes. Mod to ATX short bracket to make bridges work. Base of suppor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
    [ATX_PSU_brackets.scad, atx_brackets.stl, atx_long_bracket.stl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]
2012-12-24 Pulleys and belts now T2.5 on kit version. JHead now attached by three screws and washers. New extruder breakout PCB. Lots of instruction manual improvements from user feedback.
    [DiBond_config.scad, atx_brackets.stl, bar_clamps.stl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]
2012-12-24 Added .gitattributes to make stl files treated as binary. Removed DiBond_config.scad as filename is wrong case.
    [DiBond_config.scad]
2012-12-24 Added dibond_config.scad (correct case).
    [dibond_config.scad]
2013-03-24 Added rounded corners to some parts to make them easier to print. Filled some gaps in the X ends to make them faster to print. D motor bracket lid now one piece again, as PCB now clears it. Calibrati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
    [ATX_PSU_brackets.scad, atx_brackets.stl, atx_long_bracket.stl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]
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2013-09-25 Various design improvements: The X ends now have much stronger bar clamps and the nut traps are moved to the top for less lead screw wobble.
    X motor bracket now has two screws in the front of the motor and one at the back allowing it to be much smaller.
    The Z couplings now use neoprene tubing instead of PVC and close completely.
    The tube end caps are now nut traps to allow the tube to just have a single hole.
    The rear fixing blocks now have the central screw going the other way so have onyl two nut traps.
    The extruder springs now have washers to increase the default tension.
    The spool holder now has the washers on the outside of the spool.
    The carriage fan bracket has been strengthened.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
    [ATX_PSU_brackets.scad, alteration.csv, atx_brackets.stl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]
2013-10-01 Added Silicone tape to model and hence BOM. Updated PLA sample size to 50m. Fixed start.gcode missing from SF settings due to gitignore. Updated the manual. Assembly views moved to view folder and no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
    [bed_fan_assembly.scad, hot_end_assembly.scad, jhead_hot_end.scad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]
2013-10-29 Fixed typo in Pronterface config: the BR button was not disabling the motors. Also fixed typo in end.gcode, only a problem if code for second fan was uncommented
2013-11-18 Updated manual with instruction to fit nut and grub screw to extruder gear as no longer supplied fitted.
2014-01-12 Fixed erroneous reference to hex screws in X motor assembly.
2014-01-17 Fixed M119 showing z_min instead of z_max. Added requirement for Philips screwdriver for motor screws.
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2014-01-25 conditionally face the y-motor wires downward for thin sheets
    [y-motor-bracket.scad]
2014-02-05 Fixed Tesselation warnings by removing repeated first vertex in polygons.
    [nuts.scad, spool_holder.scad]
2014-06-11 bom.py parsing of OpenScad echo made more robust to get around bug in the MAC version of OpenScad.
2014-06-11 Fixed GT2 pulley offset and belt thickness.
    [belts.scad, pullies.scad]
2014-06-12 Mods to python scripts to allow boms and stls for accessories to be made.
    [bom.scad]
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2014-06-19 Added z_limit_switch_assembly to the list of accessories. Not recommened!
    [z_limit_switch_bracket.stl]
2014-06-21 Fixed bug in the camera bar hinge.
    [frame_edge_clamp.scad, rpi_camera_bar.stl]
2014-07-28 Added chamfer to spool holder dowels to make them easier to insert.
    [spool_holder.scad]
2014-09-17 Spool holder dowels made stronger and improved fit.
    [spool_bracket_female.stl, spool_bracket_male.stl, spool_holder.scad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]
2014-10-29 Made the RPI camera front easier to print by connecting the bottom of the clamp to the main body.
    [raspberry_pi_camera.scad, rpi_camera_front.stl]
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2015-06-14 Changed all versions to GT2 belts and pulleys
    [bar_clamps.stl, belts.scad, config.scad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]
2016-01-02 Sheets.py now removes the scad files it generates. Bodge for race condition on Win7. Note PDF files have change due to new version of InkScape but should look the same.
    [frame_base_dxf.scad, frame_gantry_and_y_carriage_dxf.scad, frame_gantry_dxf.scad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]
2016-01-03 Files genearted with new OpenScad, evrything changes but should be the same functionally.
    Modified the viewpoints for the assembly diagrams to cope with new perspective.
    [atx_brackets.stl, atx_long_bracket.stl, atx_short_bracket.stl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]
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2016-01-04 Cleaned up spool holder. Now uses offset instead of Minkowski. Dowels stronger and better fit.
    [spool_bracket_female.stl, spool_bracket_male.stl, spool_holder.scad]
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2016-01-05 Replaced minkowski with scale, child with children, and removed assign. Added thinner fan for Huxley. Added missing nut for M2 screw. Ball bearings can now position children.
    [ATX_PSU_brackets.scad, ball-bearings.scad, bulldog.scad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]
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2016-01-05 Changes for huxley. Fixing block now uses hull() instead of Minkowski() for speed. Cleaner STL for ribbon clamps.
    [bar-clamp.scad, bar_clamps.stl, d-motor_bracket.scad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]
2016-01-05 Fixed last commit
    [config.scad, d_motor_bracket.stl, d_motor_brackets.stl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]
2016-01-06 Added vero_bed config option for huxley. Moved screw sizes to vitamins.scad so it can be used stand alone. Added capped option to hole_support. Fixed bug in rounded_cylinder().
    [config.scad, utils.scad, vitamins.scad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]
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2016-01-06 Fixed cavity smaller than nut trap bug on Sturdy and Huxley.
    [bar-clamp.scad]
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2016-01-08 User space rotate added to get around OpenScad's rotate using innacurate trig functions. Eveything changes a little bit!
    [atx_brackets.stl, atx_long_bracket.stl, bar_clamps.stl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]
2016-01-08 Nut trap functions moved to nuts.scad. nut_trap_radius() and nut_trap_flat_radius() now have a horizontal flag to allow them work for vertical holes. The also have a snug flag to bodge around the fac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
    [nuts.scad, utils.scad]
2016-01-08 Reverted rounded_square change.
    [utils.scad]
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2016-01-09 Wades block made a bit stronger and now has a socket for the PTFE tube. This version used on later kits.
    [wade.scad, wades_block.stl, wades_extruder.stl]
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2016-01-10 New light and camera scheme. Removed some assigns and child for new OpenScad. Now renders the sheets for more responsive preview.
    [frame_edge_clamp.scad, light_and_camera_brackets.stl, light_strip.scad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]
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2016-01-10 Fixing block and PSU position mods for Huxley
    [main.scad]
2016-01-10 Fixed z_bar_clamp mirrored vertically in the assembly view. More noticable on Huxley as the switch holes are more offset. Updated all the assembly views for recent changes.
    [main.scad]
2016-01-10 Fixed fixing block bug introduced when assign was replaced by assigment. Fixed race condition in bom.py on Win7 with SSD.
    [main.scad]
2016-01-10 Heatsheild mods for Huxley. Has the side effect of making them all a bit bigger.
    [main.scad, y_heatshield.dxf]
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2016-01-10 Mods to carriage for Huxley. Fan duct bracket screws longer for easier removal and replacement. Direct 1.75mm drive extruder for Huxley. MK5B J-head model length corrected to match reality.
    [config.scad, direct.scad, hot_ends.scad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]
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2016-01-11 Fixed some missing STLS on Huxley
    [atx_brackets.stl, direct.scad, direct_block.stl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]
2016-01-13 Fixed some assembly views so they work for Huxley. Idler lever added to Huxley extruder. Extruders now virtual. views.py now allows camera to be specified using $vpt, $vpr and $vpd. make_machine.py n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
    [bed_fan_assembly.scad, direct.scad, direct_extruder.stl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]
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2016-01-13 Modified direct drive extruder used on Huxley to work with NEMA17 motor. Made hot end virtual.
    [direct.scad, direct_extruder.stl, extruders.scad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]
2016-01-16 Mods to support e3d in the main branch. Tweaks to the huxley extruder. Now shows hot end filament diameter on the BOM. Moved huxley spool holder back to give more room for lighting. Updated README.md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
    [config.scad, direct.scad, direct_block.stl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]
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2016-01-17 Fixed missalignment of E3D fan duct in master branch.
    [x-carriage.scad]
2016-01-19 Fan duct improvments: More clearance between belt and fan. Cleaner inner shape. Thinner walls. Fixed pinch point in one wall. Wade's screw length calculation no longer uses explicit sizes.
    [wade.scad, wades_extruder.stl, x-carriage.scad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]
2016-01-20 Fixed degenerate triangle in fan duct.
    [x-carriage.scad, x_carriage_fan_duct.stl]
2016-01-20 E3D variants now in master. Only the files that are different are present.
    [dibond_E3D_config.scad, dust_filter.stl, frame_gantry.dxf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]
2016-01-21 Fixed missing second light strip on assembly view and bom.
    [light_and_camera_brackets.stl, raspberry_pi_camera.scad, x_carriage_fan_duct.stl]
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2016-02-20 Fixed missing cross hairs on sheet drawing of RPi mounting holes on Huxley. Sheets.py can now do specified sheet.
    [frame_base.dxf, frame_gantry.dxf, frame_gantry_and_y_carriage.dxf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]
2016-02-20 No longer tries to draw the spool holder if spool is not defined.
    [main.scad]
2016-02-20 No longer makes holes for spool holder if spool is not defined.
    [main.scad]
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
